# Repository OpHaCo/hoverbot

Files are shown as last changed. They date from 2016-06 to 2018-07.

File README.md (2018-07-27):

# HoverBot : the most affordable smooth and silent two wheels drive control

**NOTE: This project is currently abandoned**  
There is more active development over at https://github.com/NiklasFauth/hoverboard-firmware-hack. We already have a working custom firmware for the hoverboard mainboard, complete with ADC, PPM and Nunchuck control. (See the linked video in the description there)

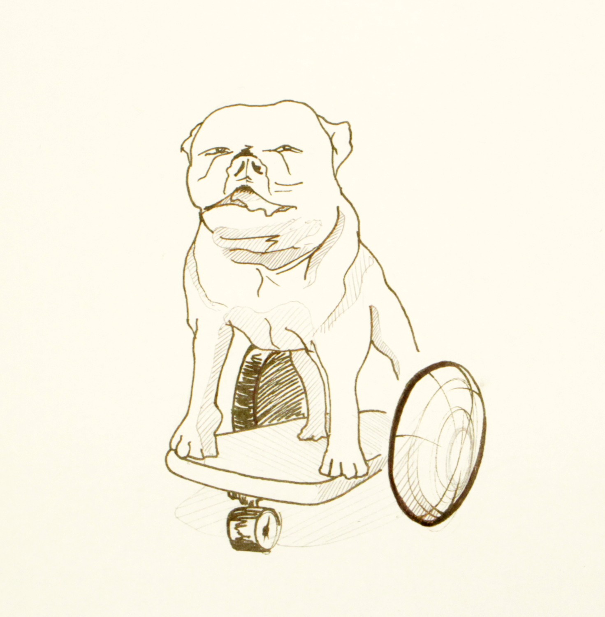
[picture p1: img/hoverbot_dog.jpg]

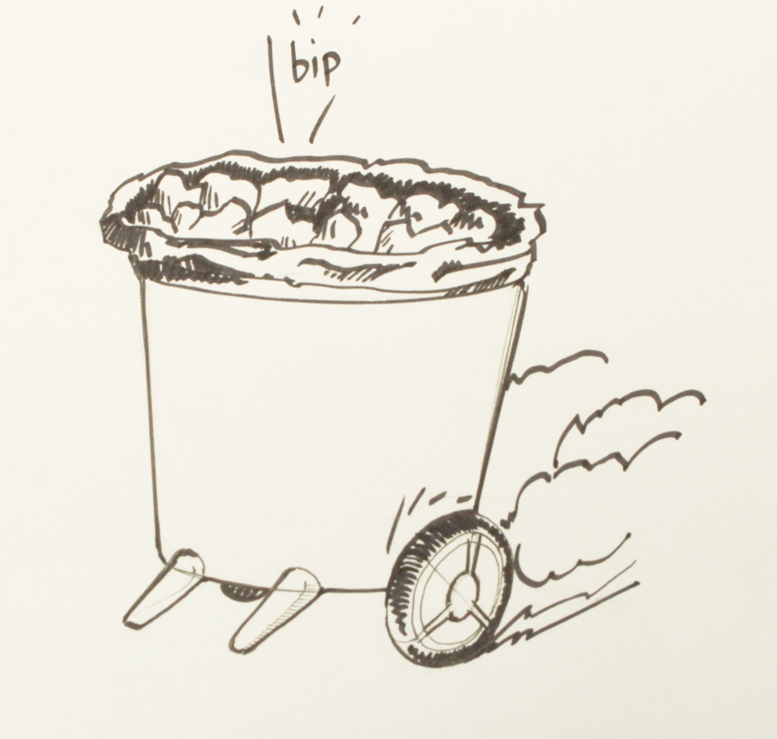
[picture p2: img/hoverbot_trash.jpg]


Project has been done in Amiqual4Home Equipex Creativity Lab - https://amiqual4home.inria.fr/

## **Description**

With hoverbot, you can do some vehicle, chassis :
 * supporting up to 264lbs (120kg). 
 * moving silently thanks to two 350W brushless motors in wheels
 * locally or remotely controlled, 
 * at an unbeatable price buying some spare parts :
    * Mother board - 55  eur
    * 36V battery  - 100 eur
    * two wheels   - 160 eur
    * additional components - 40 eur
    * **Total = 355 eur**
 * or more cheaper :
    * just buy an hoverboard and get these parts from it - 260eur
    * additional components - 40eur
    * **Total = 300eur**

Hoverboard are chinese low cost products. Low cost spare parts gives meaningful two wheels drive platform.

You don't have to be an electronic master to do it. To have motors working, you just have to connect hoverbot shield. You can either make this shield by yourself or you can get it from (TODO).

With hoverbot you will be able to drive your : 
* robot
* chair
* old dog
* couch

## **Prerequisities**

### **hardware**

* [Two hoverboard motors] (http://gyro-service.com/moteur/19-moteur.html)
* [Hoverboard mother board] (http://gyro-service.com/cirquit-carte-mere-smart-self-balancing-wheel/17-carte-mere.html)
* [36V battery] (http://gyro-service.com/batteries-samsung-smart-balance-wheel-gyropode/18-battterie-22p-samsumg-ou-de-qualite-equivalente.html)
* [hoverbot shield](#hoverbot-shield) 
* Arduino Teensy 3.1/3.2

## **Setup**

### **Components Analysis**

Refer [ifixit](http://ifixit.org/blog/7821/swagway-teardown-hoverboards/) for a detailed analysis of hoverboard components.
Interesting parts are :
 * how do these components interact?
 * is it possible to control hoverboard externally?

### **Daughterboard / motherboard communication**

Daughterboard can be used either on right/left. So we only bought 1 daughterboard to decode Daughterboard / motherboard exchanged data.
We connected the 2 motherboard / daughterboard connectors to a single motherboard.
In this case when rotating motherboard, wheels are rotating in two different direction.
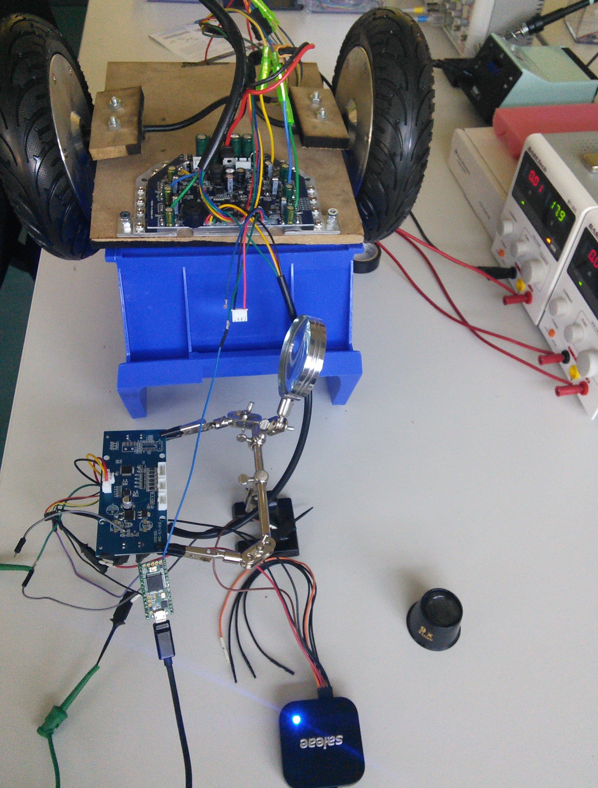
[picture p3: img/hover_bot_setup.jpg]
 

#### **Protocol**
Probing a logic analyser on daughterboard 4 wire connectors gives some interesting info :
 * logic level = 3.3V
 * bit duration ~ 38.10µs => baud rate ~ 26300kbps
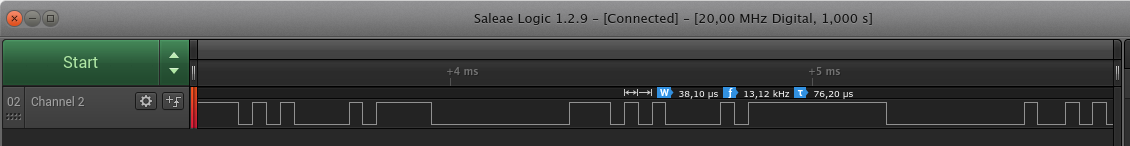
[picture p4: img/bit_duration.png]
 
 * there is no clock provided on given lines => Async protocol 
 
Is it a standard protocol? 
 * may be UART? Some clues can help... Green and yellow lines of daughterboard are connected to [STM32F103](http://www.st.com/content/ccc/resource/technical/document/reference_manual/59/b9/ba/7f/11/af/43/d5/CD00171190.pdf/files/CD00171190.pdf/jcr:content/translations/en.CD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) PA2 - UART2 TX and PA3 - UART3 RX
In order to get UART parameters : 
 * get maximum frame length taking for example a frame of 0 or a frame of 0/1/0/ and so on... After that you will conclude (helped with Salae logic ananlysers):
**Daughterboard send data to motherboard using 3.3V UART @26300bps - 1 stop bit - no parity bit.** 

#### **Exchanged data**

Here are decoded data with  UART analyzer in Salae Logic software :

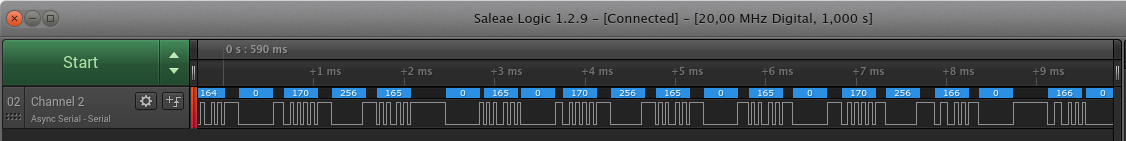
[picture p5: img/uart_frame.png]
 

Do not move daughterboard, power motherboard and read decoded data. We can see :
 * redondant 256 integer : it is frame start => frame size = 6 9bits integers

Now let's play with photodiode used in daughterboard contacts :
 * if we hide at least one of it  last frame integer = 85
 * otherwise last frame integer = 170
If 170 value is sent to motherboard : motors won't be driven (it means user to not have its feet on hoverboard) (it means user to not have its feet on hoverboard)
 
4 remaining bytes must be decoded : two of these bytes repeats.
Rotating daughterboard gives indication :
 * little move only modify a frame integer => this integer must be low significant 9bit 
 * more rotation modifies other integer    => rotation seems to be encoded on 2 9 bit integers.
Rotating around 0 helps us :
**Angular value is coded in 2x9bits signed integer value (2's complement)**

We can check it is only an angular value applying linear acceleration to daughterboard. In this case angular value do not change.

#### ** Speed sensor **
In wheels some hall sensors are used to get wheel speed (3 sensors per wheel).
On mother board, sensor pulses are filtered using an RC filter. To get speed, we must connect it to hoverbot. 

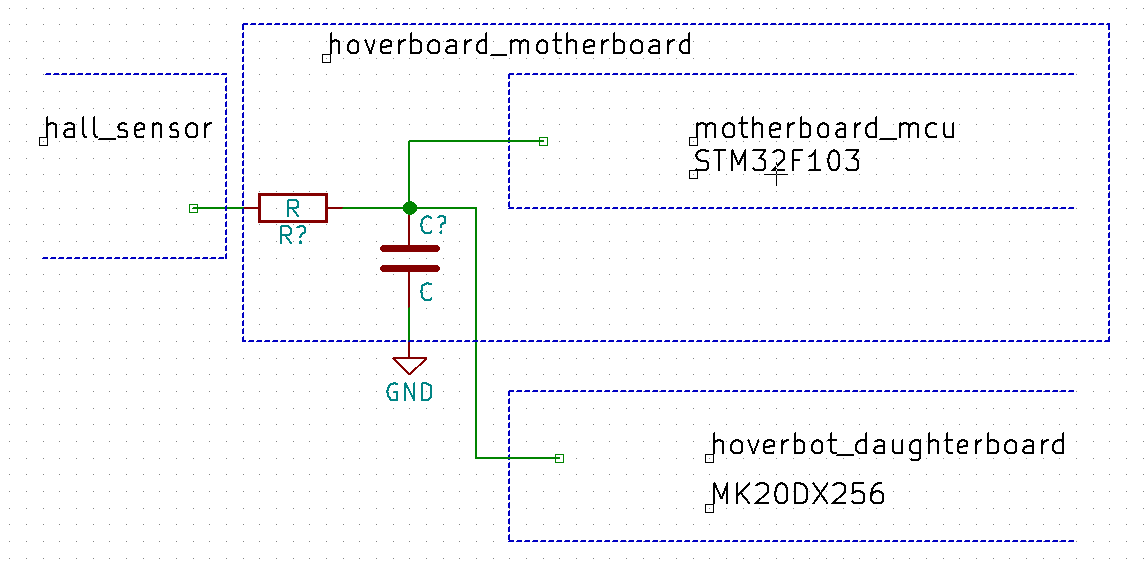
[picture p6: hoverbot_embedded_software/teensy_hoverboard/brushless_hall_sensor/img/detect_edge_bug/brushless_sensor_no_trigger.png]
 

If we trigger a digital output (channel 0) on a rising edge (channel 0) we do not have a clean signal :
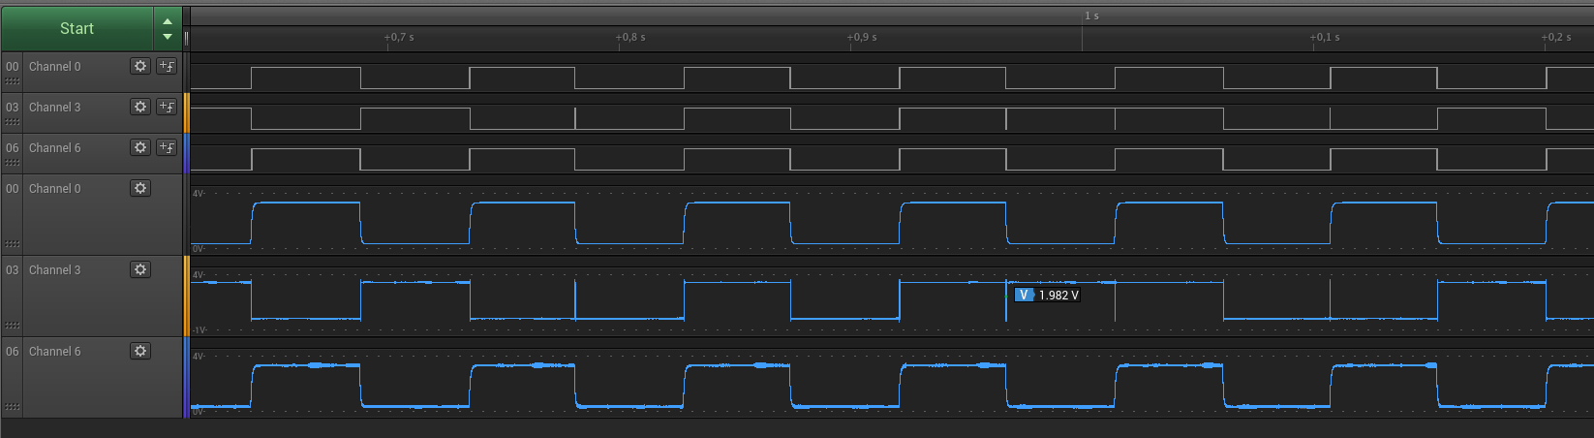
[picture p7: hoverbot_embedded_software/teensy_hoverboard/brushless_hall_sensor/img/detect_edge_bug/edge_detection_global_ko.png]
 

With a zoom :
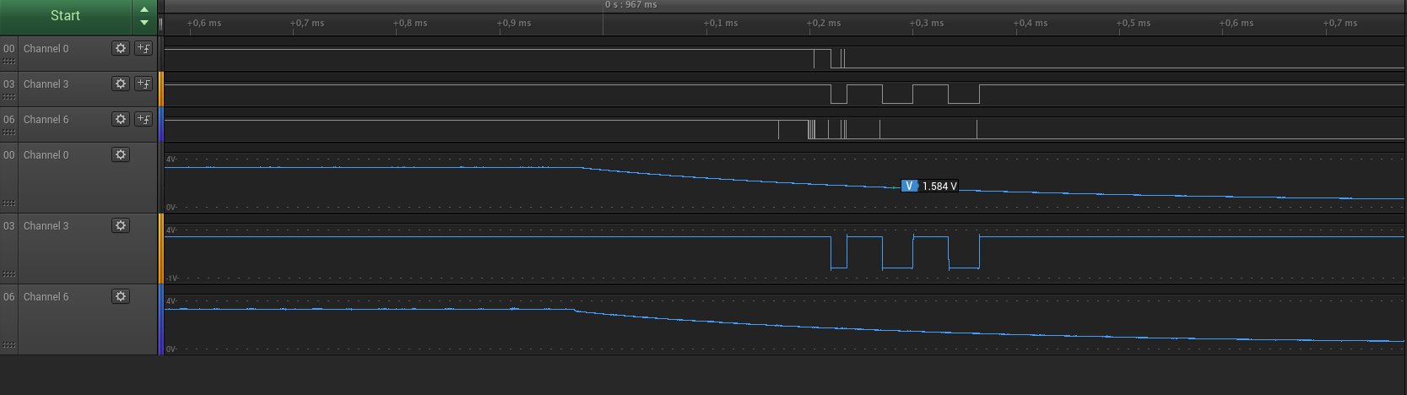
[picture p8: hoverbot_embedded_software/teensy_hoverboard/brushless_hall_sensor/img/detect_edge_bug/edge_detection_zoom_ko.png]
 

Small oscillation when V=Vdd/2 generates some falling /rising edges. Because of RC time constant, we can get lot of oscillations leading to some false detections. It could be software filtered (either using timer or checking multiple times read value). As I prefer capturing Hall sensor pulses using external interrupt it is better to have an hardware solution. As Teensy MCU does not have any input schmitt trigger we will add it :

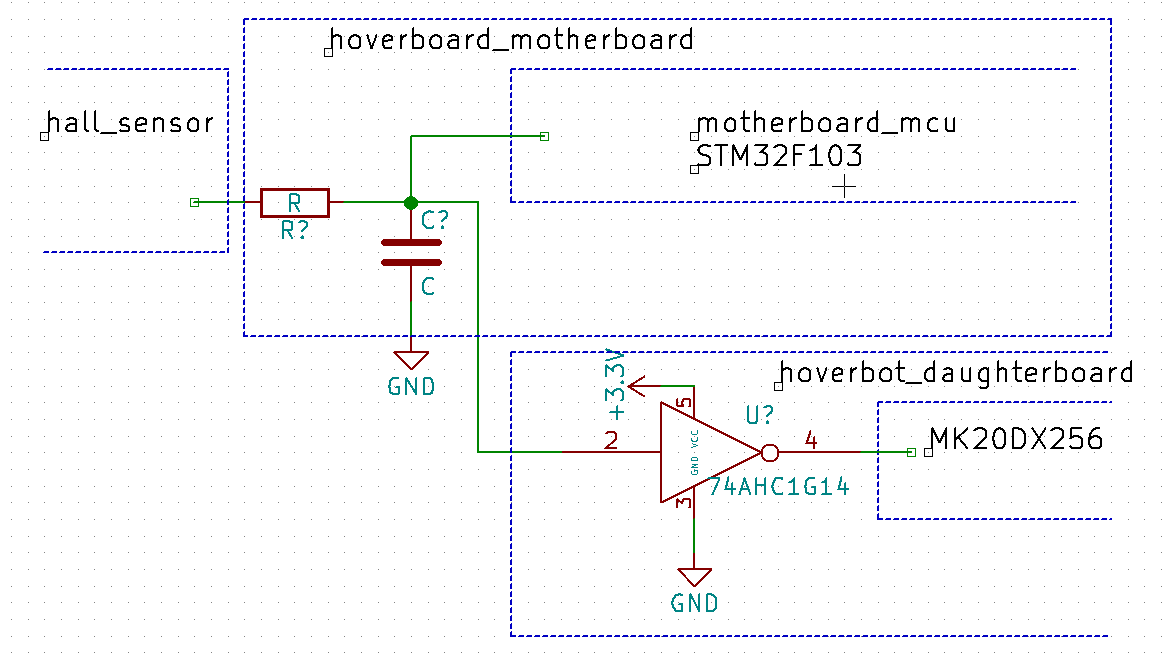
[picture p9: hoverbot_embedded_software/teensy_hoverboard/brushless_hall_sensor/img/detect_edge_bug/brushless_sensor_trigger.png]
 

After we have a good pulse detection :

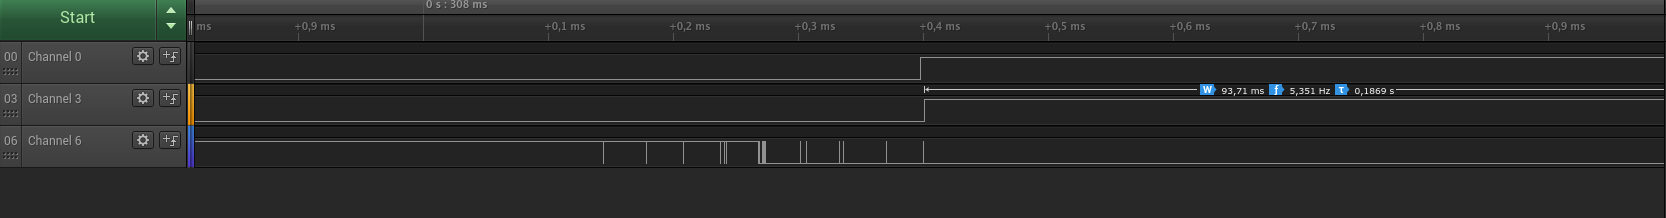
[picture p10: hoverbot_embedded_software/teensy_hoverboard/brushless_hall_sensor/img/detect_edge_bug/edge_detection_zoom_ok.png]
 
 
### **hardware** 

In order to control hoverboard we need an external MCU to :
 * send left and right foot angular position => we need two UART Tx lines supporting 9bits UART @ 26300bps
 * optionally read daughterboard current postion (for tests) => we need 1 UART Rx line supporting 9bits UART @ 26300bps
 
Different MCU can be used, we could use UART bitbanging libraries... But a nice solution is to use teensy 3.1/3.2 :
 * it runs @3.3V
 * [9 bit uart supported on Arduino Core] (https://www.pjrc.com/teensy/td_uart.html)
 * 3 avaialble hardware UARTs!

### **software** 

#### Prerequisities
##### Enable 9-Bit UART on Teensy
Edit :

    your_arduino_core_folder/hardware/teensy/avr/cores/teensy3/HardwareSerial.h

Uncomment :

    #define SERIAL_9BIT_SUPPORT

##### Add needed libraries
Several libraries are provided in this repo : 
 * hoverboard : hoverboard control / feddbacks
 * brushless_hall_sensor
 * logger 

If you use arduino IDE, you must create symlinks/shortcuts from these libraries path to Arduino library folder :

    ln -s your_folder/hoverbot/hoverbot_embedded_software/teensy_hoverboard/hoverboard arduino_user_path/libraries/
    ln -s your_folder/hoverbot/hoverbot_embedded_software/teensy_hoverboard/brushless_hall_sensor arduino_user_path/libraries/
    ln -s your_folder/hoverbot/hoverbot_embedded_software/teensy_hoverboard/logger arduino_user_path/libraries/

Then from Arduino IDE add these libraries.

##### Configure logging level
    
Edit 
    your_folder/hoverbot/hoverbot_embedded_software/teensy_hoverboard/logger/logger_config.h
    
and set needed log level (refer your_folder/hoverbot/hoverbot_embedded_software/teensy_hoverboard/logger/README.md)
    
### Arduino sketch

As we saw in our first tests, when same daughterboard is connected to two motherboards/daughterboard connectors :
 * wheels rotating direction is different. Hoverboard is rotating
In this case same angular value on left foot and right foot is sent to motherboard.
In order to have hoverboard moving forward / backward we must apply for example :
 * a positive angular value on right foot daughterboard Uart
 * negative angular value on left foot daughterboard Uart

From that  simple code is provided here :
[Refer code](https://github.com/OpHaCo/hoverbot/blob/master/hoverbot_embedded_software/teensy_hoverboard/teensy_hoverboard.ino)
In `echoGoForward()`  function : it reads current angular value from daughterboard to control hoverboard in forward direction.

After testing we can easily : 
 * control speed of both wheels when it is rotating in different direction (under load or not)

But we cannot :
 * control speed of both wheels when it is rotating is same directions (not under load). **In this case, motors reach needed value but quickly speed up until max speed**
 
We can suppose, closed loop algorithm on motherboard does not support forward / backward mooving when it is not under load.

## Interfaces
### UART

Hoverboard control over UART can be done running :

    python3 your_folder/hoverbot/hoverbot_gateway_software/examples/hoverboard_uart_control/hoverboard_uart_control.py -p TEENSY_PORT
    
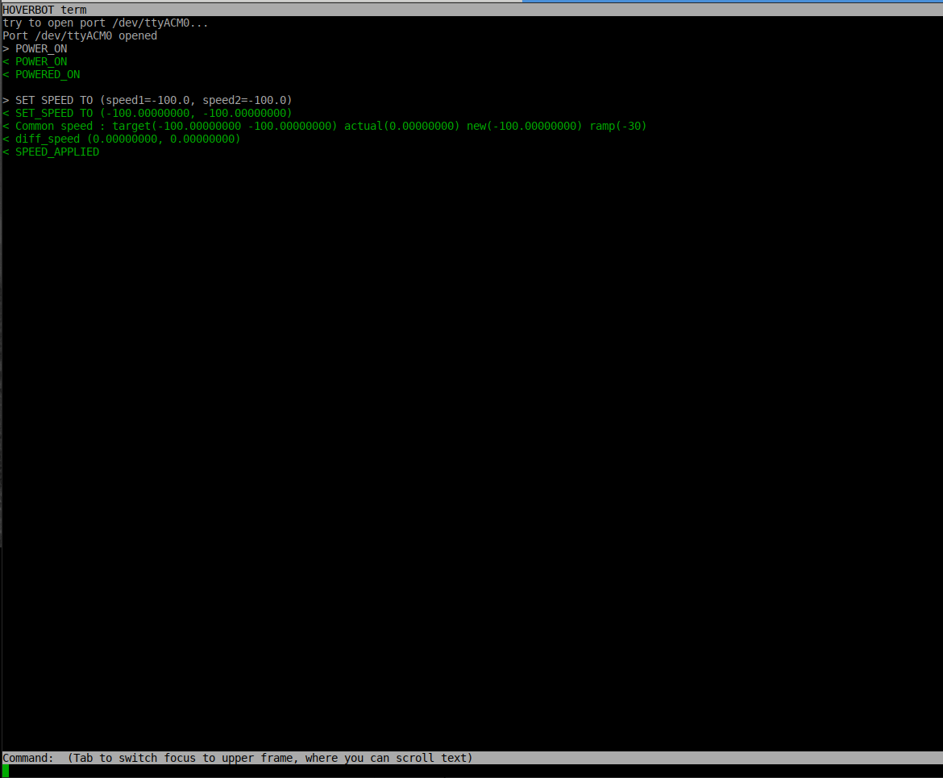
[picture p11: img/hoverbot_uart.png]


#### Supported commands :

    power_on

    power_off
    
    set_speed motor1_value motor2_value
    
    x // Manual keyboard control => hoverbot controlled using numeric pad

### SPI
### Wifi
### BLE

## Commands
TODO

### Control commands
TODO
###ROS
## Events
TODO

## Hoverbot shield
### PCB design

## Examples
### Racing chair

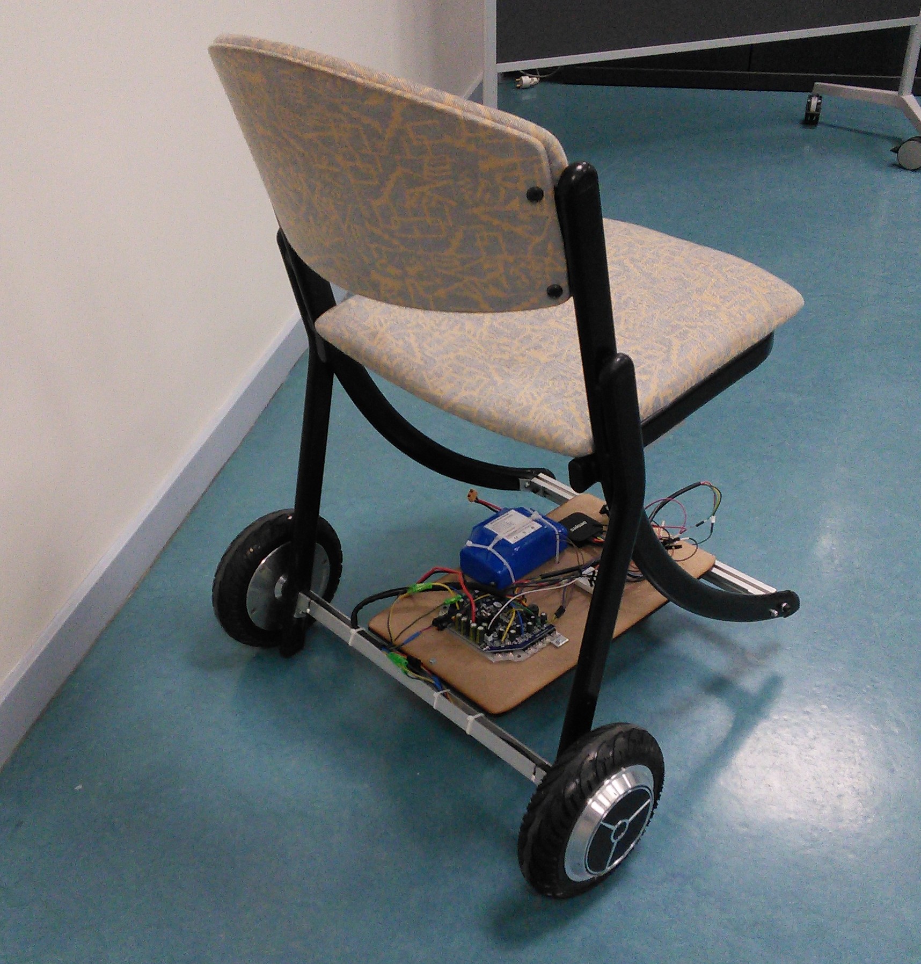
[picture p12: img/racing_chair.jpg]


## Issues

## References
* http://www.electronicspoint.com/threads/reverse-engineering-a-hoverboard-with-wheels-accelerometer.279098/
* http://drewspewsmuse.blogspot.fr/2016/06/how-i-hacked-self-balancing-scooter.html
* https://developer.mbed.org/users/Thomas_H/code/HoverboardTest/

## Next steps

* improve hoverboard control
* continue cleaning (remove some unused attributes in hoverboard)
* add PID : measure reliable speed from hall sensors
* use all days a reliable racing chair
* make hoverbot shield : deliver CAD
* ROS compatible?
* get error status

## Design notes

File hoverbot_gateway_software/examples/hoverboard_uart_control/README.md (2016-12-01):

# Description
Example of hoverboard UART control.

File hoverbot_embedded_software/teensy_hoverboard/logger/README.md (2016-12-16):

## logging

### Overview

Logging library, supports a variable list of arguments and its format specifiers. 
Log level can be modified according to user needs. 
Using preprocessor logging macros defined in logger.h reduces code size depending on selected logger level.

#### Supported targets

  * MCU having Arduino software (Stream, Serial...)

####Log levels
 * LOG_LEVEL_NOOUTPUT 
 * LOG_LEVEL_ERRORS 1
 * LOG_LEVEL_INFOS 2
 * LOG_LEVEL_DEBUG 3
 * LOG_LEVEL_VERBOSE 4

#### Code snippet
Log using a software serial stream.

    #include <logger.h>
    #include <AltSoftSerial.h>
    
    #define LOG_LEVEL LOG_LEVEL_DEBUG
    
    static AltSoftSerial altSerial;

    void setup()
    {
        Serial.begin(115200);
        altSerial.begin(9600);
        
        LOG_INIT(LOG_LEVEL, &altSerial);
	    LOG_INFO(F("application started ! \n"));
    }

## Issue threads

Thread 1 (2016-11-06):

Speed control loop

tyler123durden, 2016-11-06:
Hello,
I've also started with some hoverboard hacks, here are my projects:
https://github.com/tyler123durden/hoverboard-hardware
https://developer.mbed.org/users/Thomas_H/code/HoverboardTest/

I started some tests with a closed loop control for the speed. But at certain points I've got some strange behaviour. Especially when wheels should rotate in different directions or speeds. It is possible to do this but control loop behaves kind of sluggish. Do you have done such tests?
Here are some diagrams:
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

Lahorde, 2016-11-17:
As you can see, in my sketch I control both motors. I can :

* rotate cleanly motor 1 in clockwise while motor 2 is in other direction (in this case, I send same angle values to mother board)
* rotate cleanly motor 1 in non-clockwise while motor 2 is in other direction (in this case, I send same angle values to mother board)
in these configurations, I can control motor speed.

But when I have both motors rotating in same direction (in this case I give a positive angular position on left daughterboard UART and a negative one on right daughterboard UART), first it rotates well, but after some seconds, it speeds up until reaching max speed. I think something misses in this case. It's quite strange, I'm wondering if my motherboard is not buggy. May be solution is elsewhere : calibration, other sensor...
I've tried different calibrations values and it dit not change anything. I told Drew Nibble if he got same issue and he said "I believe that the acceleration when both wheels are going the same direction is a bug in the closed loop controller. It does not seem to happen under load (although I have not tested extensively)"
 I must test this hypothesis on a true hoverboard! May be you have tested it?

So I should get in few days a new motherboard : http://www.skywalkers.paris/pieces-detachees-hoverboard/91-carte-mere-taotao-hoverboard-adulte-7091046701306.html
and an hoverboard.

I think we want to make same thing : closed loop speed control using this cheap motherboard, and I'm sure we will manage to do it!

tyler123durden, 2016-11-17:
OK, I see. In my tests same direction means different sign for both sides and different direction (hoverboard rotates) means same sign.
The motor board seems to have kind of PI characteristic. As you see in same direction plot. You have to reduce input to 0 or nearly to hold same speed. I think this is your speed up at constant input.
But this does not apply for different directions (same sign). Here it has more kind of P characteristic. Which does also apply if both wheel speeds differ to much then.
Will try to get some plots for open loop speed response. But maybe I've got another firmware version because I must send following sequence, which has 2 more bytes.

            oMotorRight.putc(256);
            oMotorRight.putc(_Controlloop[RIGHT].u & 0xFF);
            oMotorRight.putc((_Controlloop[RIGHT].u >> 8) & 0xFF);
            oMotorRight.putc(_Controlloop[RIGHT].u & 0xFF);
            oMotorRight.putc((_Controlloop[RIGHT].u >> 8) & 0xFF);
            oMotorRight.putc(85);
            oMotorRight.putc(82);
            oMotorRight.putc(82);

I've not tested my setup under load, will try to test it that weekend.

Lahorde, 2016-11-17:
" As you see in same direction plot. You have to reduce input to 0 or nearly to hold same speed.", that's it, above a given threshold, speeds keeps increasing until reaching max speed. You are true with PI behaviour, but physically, it's quite hard to understand, but I think it's because I never rode an hoverboard. Maybe in forward direction, rotating feets rotate first gyroscope daughterboards causing hoverboard speed up, maybe during this acceleration gyroscope daughteboards come back to a flat position... I should test it in some few days!

Lahorde, 2016-11-17:
I will test tomorrow an integral control,
In pseudo code :

    setForwardSpeed(speed)
       setRightSpeed(speed*ramp_up_coef)
       setLeftSpeed(speed*ramp_up_coef)
       startTimer(duration = 1/ramp_up_coeff)

    onTimerExpired()
       setRightSpeed(0 calibration value)
       setLeftSpeed(0 calibration value)

Lahorde, 2016-11-18:
Got it and tested :
```
/**
 * Integral control of speed
 */
void goForward(uint16_t speed)
{
  float RAMP_UP_FACTOR = 1;
  uint16_t  speedRampUp = (speed*RAMP_UP_FACTOR);

  uint16_t lFrame[6] = {256, speedRampUp & 0xff, speedRampUp >> 8 & 0xff, speedRampUp & 0xff, speedRampUp >> 8 & 0xff, 85};
  uint16_t rFrame[6] = {256, (-speedRampUp) & 0xff, (-speedRampUp) >> 8 & 0xff, (-speedRampUp) & 0xff, (-speedRampUp) >> 8 & 0xff, 85};

  Serial.print(millis());
  Serial.print(": applying speed of ");
  Serial.println(speedRampUp);

  uint32_t timeStart = millis();
  while((millis() - timeStart) < (1/RAMP_UP_FACTOR)*10000)
  {
    for(uint8_t index = 0; index < 6; index++)
    {
      DAUGHTER_BOARD_SERIAL_SIM_R.write9bit(rFrame[index]);
      DAUGHTER_BOARD_SERIAL_SIM_L.write9bit(lFrame[index]);
    }
  }

  speedRampUp = _calValue;

  lFrame[1] = _calValue & 0xff;
  lFrame[2] = _calValue >> 8 & 0xff;
  lFrame[3] = lFrame[1];
  lFrame[4] = lFrame[2];

  rFrame[1] = -_calValue & 0xff;
  rFrame[2] = -_calValue >> 8 & 0xff;
  rFrame[3] = rFrame[1];
  rFrame[4] = rFrame[2];

  Serial.print(millis());
  Serial.print(": applying speed of ");
  Serial.println(_calValue);

  while(1){
    for(uint8_t index = 0; index < 6; index++)
    {
      DAUGHTER_BOARD_SERIAL_SIM_R.write9bit(rFrame[index]);
      DAUGHTER_BOARD_SERIAL_SIM_L.write9bit(lFrame[index]);
    }
  }
}
```

In order to get clean control we must also hack calibration process to have a 0 calibration!

Lahorde, 2016-11-18:
Look at https://github.com/OpHaCo/hoverbot/blob/master/hoverbot_embedded_software/teensy_hoverboard/teensy_hoverboard.ino for an updated code. Some work in code must be done to have a clean control, I will close issue when I will finish it.

tyler123durden, 2016-11-18:
Great to see it works!
So maybe you could also try controlling both wheels with different speeds and look at the response.
For the calibration process if would guess all is done in the motor controller and no communication to the gyro board is done. The motor board just sets the zero point to the received gyro inputs. So just send 0 to the motorboard and start calibration should do the trick.
As mentioned above a simple PI controller works quite good for speed control except if wheel speed differs to much.

Lahorde, 2016-11-19:
Yes, calibration can definitely been done manually, as you said,  just set a 0 output on your MCU UARTs when you do calibration. Next week I will test it deeper, integration factor must be precisely identified.

KevinPlaridel, 2016-12-11:
Hello Lahorde. I've been trying to make my hoverboard works and I tried your sketch, but there is error. Can you help me?

I put the hoverboard.h and brushless_hall_sensor.h in
C:\Program Files (x86)\Arduino\hardware\teensy\avr\cores\teensy3

but the error is
```
C:\Program Files (x86)\Arduino\hardware\teensy\avr\cores\teensy3\hoverboard.cpp:81:33: error: 'SERIAL_9N1' was not declared in this scope
   _p_gyro1Serial->begin (26300, SERIAL_9N1);  // 9 bits mode
                                 ^
C:\Program Files (x86)\Arduino\hardware\teensy\avr\cores\teensy3\hoverboard.cpp: In member function 'Hoverboard::EHoverboardErr Hoverboard::setSpeed(float, float)':
```

Hope you can help. Thank you

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

KevinPlaridel, 2016-12-11:
SERIAL_9N1 is solved. but when I added
```
#include <hoverboard.h>
#include <brushless_hall_sensor.h>
```
"idlecontrol() was not declared" said in the error

```
hoverboard_original:36: error: 'idleControl' was not declared in this scope
     idleControl();
```

Lahorde, 2016-12-16:
I've updated code, refer https://github.com/OpHaCo/hoverbot/blob/master/hoverbot_embedded_software/teensy_hoverboard/hoverboard/hoverboard.cpp
I've not yet implemented any PID. Some coding / cleaning must still be done but now everything is possible. Next step is to improve hoverboard control and to make an hoverbot shield.

Closed 2016-12-16.

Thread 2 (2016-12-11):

Error Compiling

KevinPlaridel, 2016-12-11:
I can't compile the sketch because there's an error to hoverboard.cpp and idlecontrol().
I added the .cpp and .h in

> C:\Program Files (x86)\Arduino\hardware\teensy\avr\cores\teensy3

this is the error:
```
In file included from C:\Users\Kevin\Documents\School\thesis\sketch\hoverboard\hoverboard.ino:2:0:

C:\Program Files (x86)\Arduino\hardware\teensy\avr\cores\teensy3/hoverboard.cpp: In member function 'Hoverboard::EHoverboardErr Hoverboard::init()':

C:\Program Files (x86)\Arduino\hardware\teensy\avr\cores\teensy3/hoverboard.cpp:81:33: error: 'SERIAL_9N1' was not declared in this scope

   _p_gyro1Serial->begin (26300, SERIAL_9N1);  // 9 bits mode

                                 ^

C:\Program Files (x86)\Arduino\hardware\teensy\avr\cores\teensy3/hoverboard.cpp: In member function 'Hoverboard::EHoverboardErr Hoverboard::setSpeed(float, float)':

....

Error compiling for board Teensy 3.2 / 3.1.
```

Lahorde, 2016-12-11:
Open :

    your_arduino_core_folder/hardware/teensy/avr/cores/teensy3/HardwareSerial.h

Uncomment

    #define SERIAL_9BIT_SUPPORT

Closed 2016-12-11.

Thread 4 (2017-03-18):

Documentation of power button and stat wiring

MaxZZZZZZ, 2017-03-18:
Thanks for the code that you provided, it's very useful.
One thing that is missing in the README is how you wired power button and status LED. Can you please add it or at least respond in this issue?

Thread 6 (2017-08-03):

OpenSource firmware for motor control on the STM32F103

casainho, 2017-08-03:
Hi, great project!!

I developed OpenSource firmware for motor control using the STM32F103, for electric unicycles. Currently I am developing for the cheap chinese ebike controllers, one based on STM8 and other with STM32F103.

Would be great if you or someone could develop firmware for the motor control for the hoverboards.

But my target is to make firmware for cheap ebike Kunteng STM8 controllers and make them a general bldc motor controller - it has UART communication and so with an Arduino, anyone could control easily this type of motors.

https://opensourceebikefirmware.bitbucket.io/

https://eggelectricunicycle.bitbucket.io/

LeoDJ, 2017-09-10:
I would really like to delve into developing a BLDC controller on the hovervoard mainboard.
But I do not know how to best get started and not brick and/or fry the motherboard. E.g. if I would activate the wrong outputs, the MOSFETs would short the battery and something will explode.

Also I'm not quite sure how I would then implement the BLDC controller using the hall effect sensor inputs.

I guess, that you have way more experience with those things, seeing that you already wrote such a firmware for the STM, only driving one motor.

Maybe we could work together on this? I am currently in the process of reverse engineering the mainboard (getting the pinout of the mosfets etc)

casainho, 2017-09-10:
Hi.

_Maybe we could work together on this? I am currently in the process of reverse engineering the mainboard (getting the pinout of the mosfets etc)_
I am not motivated to work on the hoverboard: I look to them as a toy because are instable after 10km/h; I would prefer electric unicycles that can go over 30km/h (yes, I did ride both of them). But now I even prefer electric bicycles because they are way safe than electric unicycles at speeds like 25km/h and over than. I usually ride at up to 45km/h, on flat land were I live.

My focus is to develop OpenSource firmware for the cheap and widely available EBike motor controllers. The one I am developing for now, costs only 14€!! It has UART interface for an LCD or bluetooth modules. My plan is to create a generic motor controller that can be commanded by Arduino, using the UART interface, then anyone will be able to this motor controllers and do oter devices like hoverboard, electric unicycles, etc!!

I have an idea for you: use the Lishui LSW-675 EBike motor controller that is relative cheap and uses the same STM32FEBKC6T6 as on the hoverboard -- you can find the datasheet of STM32FEBKC6T6 here as many other information: https://opensourceebikefirmware.bitbucket.io/Motor_controllers--Lishui_motor_controllers--LSW-675.html

Good luck and don't forget to start a thread on https://endless-sphere.com/forums/viewforum.php?f=30 to document and post news about this project!!

LeoDJ, 2017-09-28:
Okay. On terms of hoverboard riding, we are on the same page. I don't want to use it in its original form, but repurpose the motors, main board and battery as a drive chain for a few robot ideas I have in mind, because they are still very powerful.
I think I found the [official firmware](https://github.com/EGG-electric-unicycle/bldc_chinese_firmware_2) for the hoverboard mainboard, so it hopefully shouldn't be so hard to reprogram it to accept direct control commands over UART.

Thanks for the tip with the LSW-675. It's too expensive for me to use as an ESC for the two motors, but I'll look into the firmware for inspiration.

As for the 14€ open source motor controller: That sounds really neat, I'll look forward to using that in the future 😉

casainho, 2017-09-28:
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
Don't you want to join the project?? we can implement the firmware for a
generic motor controller that is controlled using UART commands send by
Arduino.

--
Cumprimentos,
Jorge Pinto
E-mail: casainho@gmail.com
Telemóvel: 927145983

LeoDJ, 2017-09-28:
Yeah, good idea.
Currently I'm a little bit busy with uni, but I'll see when I got time :D
What do you think is the best way we can communicate?

casainho, 2017-09-28:
We use the forum, see on the project page the link.

Em 28/09/2017 16:39, "Leandro Späth" <notifications@github.com> escreveu:

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

chulo601, 2017-10-14:
LeoDJ i have over 50+ hoverboard i can give for free just pay for shipping so you can test the reprogramming of the hoverboard. I will like to use the hoverboard main board and be able to control both wheels with arduino.
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

LeoDJ, 2017-10-14:
Wow, that sounds awesome! It would be neat to have one or two that I can test my code on, without the fear that I would be bricking one beyond repair ^^
How much would shipping to Germany cost?

VladimirAkopyan, 2017-11-02:
this is very amusing

ScottEllisNovatex, 2018-05-01:
See https://github.com/NiklasFauth/hoverboard-firmware-hack

vetalik08, 2018-05-28:
Have any more hover boards your willing tk donate if I paid for shipping?

eric-schleicher, 2018-06-06:
@chulo601 is this still an area of interest for you?  I have a number of interns that are interested making a balance bot from these component. let me know if there is still a supply of yunked parts.  we're in US, would certainly pay for shipping.

casainho, 2018-06-11:
I implemented FOC using as input: battery voltage; actual duty_cycle; battery current read on shunt; motor speed in ERPs measured on hall sensors; motor inductance.

Videos and realtime graphs, etc:
- https://www.endless-sphere.com/forums/viewtopic.php?p=1385495#p1385495
- https://www.endless-sphere.com/forums/viewtopic.php?p=1385495#p1385553

The only parameter that depends from the motor is the motor inductance L. The math is:
angle = arc sin (I motor phase * W * L / V motor phase).
I motor phase: battery current read on shunt / duty_cycle
V motor phase: battery voltage * duty_cycle

The piece of code:
  //************************************************************************************
  // FOC implementation by calculating the angle between phase current and rotor magnetic flux (BEMF)
  // 1. phase voltage is calculate
  // 2. I*w*L is calculated, where I is the phase current. L was a measured value for 48V motor.
  // 3. inverse sin is calculated of (I*w*L) / phase voltage, were we obtain the angle
  // 4. previous calculated angle is applied to phase voltage vector angle and so the
  // angle between phase current and rotor magnetic flux (BEMF) is kept at 0 (max torque per amp)

  // calc E phase voltage
  ui16_temp = ui16_adc_battery_voltage_filtered * ADC10BITS_BATTERY_VOLTAGE_PER_ADC_STEP_X512;
  ui16_temp = (ui16_temp >> 8) * ui8_duty_cycle;
  ui16_e_phase_voltage = ui16_temp >> 9;

  // calc I phase current
  if (ui8_duty_cycle > 10)
  {
    ui16_temp = ui16_adc_battery_current_filtered * ADC_BATTERY_CURRENT_PER_ADC_STEP_X512;
    ui32_i_phase_current_x2 = ui16_temp / ui8_duty_cycle;
  }
  else
  {
    ui32_i_phase_current_x2 = 0;
  }

  // calc W angular velocity: erps * 6.3
  ui32_w_angular_velocity_x16 = ui16_motor_speed_erps * 101;

  // 36V motor: L = 76uH
  // 48V motor: L = 135uH
  ui32_l_x1048576 = 142; // 1048576 = 2^20

  // calc IwL
  ui32_temp = ui32_i_phase_current_x2 * ui32_l_x1048576;
  ui32_temp *= ui32_w_angular_velocity_x16;
  ui16_iwl_128 = ui32_temp >> 18;

  // calc FOC angle
  ui8_foc_angle = asin_table (ui16_iwl_128 / ui16_e_phase_voltage);

  // low pass filter FOC angle
  ui16_foc_angle_accumulated -= ui16_foc_angle_accumulated >> 4;
  ui16_foc_angle_accumulated += ui8_foc_angle;
  ui8_foc_angle_filtered = ui16_foc_angle_accumulated >> 4;

  // apply FOC angle
  ui8_foc_angle_correction = -ui8_foc_angle_filtered;
  //************************************************************************************

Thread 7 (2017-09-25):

Hoverboard shield

hermanbanken, 2017-09-25:
Hi guys,
For a hackathon I'm currently figuring out what is gonna drive our (potentially large/heavy) robot, so I'm looking beyond robot chassis and looking to this kind of projects. Unfortunately I'm no electronisch expert, so I'm relying on what I can find here and there.

Do I get it right that you intent to design a shield and this image contains the prototype on the breadboard?
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

Could you share a photo where you can see the actual breadboard? Also is it correct you have a Logic Analyzer on there? Is it required?

Hope you can share some more of your efforts!

plguhur, 2017-11-02:
Hello guys, I am looking quite for the same thing: the hoverbot shield. Did you publish your PCB design?

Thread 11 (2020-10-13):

driving one motor

setaretavakoli, 2020-10-13:
hi
could you help us to drive only one motor?
because doe to our search the controller circuit needs both of the motors to have a close circuit.
pls. correct us if we're wrong.
you can contact us with :
kakimia595@gmail.com or f.tavakoli9273@gmail.com

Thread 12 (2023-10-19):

Denver need help

r3k0sa, 2023-10-19:
Hey maybe sameone have model:DBO-10000 mk3 software? I made a mistke when trying edit and make it with remote control... i dont saved software and now its not working so plz if someone have send it to me 🙏
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

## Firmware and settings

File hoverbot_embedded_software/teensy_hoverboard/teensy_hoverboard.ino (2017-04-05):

/******************************************************************************
 * @file    hoverboard sketch
 * @author  Rémi Pincent - INRIA
 * @date    28/11/2016
 *
 * @brief Hoverboard sketch example to control hoverboard.
 *  
 * Project : hoverbot
 * Contact:  Rémi Pincent - remi.pincent@inria.fr
 *
 * Revision History:
 * https://github.com/OpHaCo/hoverbot.git
 * 
 * LICENSE :
 * hoverbot (c) by Rémi Pincent
 * project_name is licensed under a
 * Creative Commons Attribution-NonCommercial 3.0 Unported License.
 *
 * You should have received a copy of the license along with this
 * work.  If not, see <http://creativecommons.org/licenses/by-nc/3.0/>.
 *****************************************************************************/

/**************************************************************************
 * Include Files
 **************************************************************************/
#include <logger_config.h>
#include <hoverboard.h>
#include <brushless_hall_sensor.h>

/**************************************************************************
 * Manifest Constants
 **************************************************************************/
#define LOG_SPEED 500000
#define LOG_SERIAL Serial
#define MAX_CMD_LENGTH 0xFFU

#define SET_SPEED_CMD_LENGTH 13U 
#define POWER_ON_CMD_LENGTH   1U 
#define POWER_OFF_CMD_LENGTH  1U 
#define STOP_CMD_LENGTH       1U 
/**************************************************************************
 * Type Definitions
 **************************************************************************/
/*****************************************
 * CONTROL cmd format
 *  __________________________________
 * |       |             |            |
 * |CMD_ID | CMD_PARAMS  | TODO CRC   |
 * |_______|_____________|____________|
 * 
 ****************************************/
typedef enum
{
  SET_SPEED    = 0, /* ARGS : SPEED1 (short LE) - SPEED2 (short LE) */
  POWER_ON     = 1,
  POWER_OFF    = 2,
  STOP         = 3
}EControlCmd;

typedef enum
{
  ACK          = 0,
  SPEED_STATUS = 1
}EFeedbackCmds;

typedef enum
{
  ACK_OK        = 0, 
  ACK_BAD_STATE = 1
}ECmdAckType;

/**
 * Class that listen hoverboard commands over UART to control it.
 */
class HoverboardListenerExample : public HoverboardListener
{
  public:
    HoverboardListenerExample(Hoverboard* );
    void init(void);
    void calibrateHoverboard(void);
    void onSpeedChanged(float arg_f_motor1Speed, float arg_f_motor2Speed);
    void onSpeedApplied(void);
    void onPowerOn(void);
    void onPowerOff(void);
    void pollCmd(void);
    void sendCmd(EFeedbackCmds arg_e_cmdType, uint8_t arg_au8_cmd[], uint8_t arg_u8_cmdLength);
    
  private:
    void waitKey(uint8_t arg_u8_key);
    void handleCommand(uint8_t arg_u8_cmd[], uint16_t arg_u16_cmdLength);

  private:
    Hoverboard* _p_hoverboard;
};

/**************************************************************************
 * Static variables definitions
 **************************************************************************/
static uint8_t _au8_rcvCmd[MAX_CMD_LENGTH] = {0};

/** ItCBS will be filled by hoverboard */
static BrushlessHallSensor::ItCbs motor1ItCbs;

/** Hall sensor 1 - Give pin here */
static BrushlessHallSensor::Config _hallSensor1Conf(17, 18, 19, motor1ItCbs);

/** ItCBS will be filled by hoverboard */
static BrushlessHallSensor::ItCbs motor2ItCbs;

/** Hall sensor 2 - Give pin here */
static BrushlessHallSensor::Config _hallSensor2Conf(13, 14, 15, motor2ItCbs);

static Hoverboard::Config _hoverboardConf(20, 
  21,
  &_hallSensor1Conf,
  &_hallSensor2Conf,
  Serial1,
  Serial3);

static Hoverboard _hoverboard(_hoverboardConf);
static HoverboardListenerExample _hoverboardListenerExample(&_hoverboard);
/**************************************************************************
 * Global functions Definitions
 **************************************************************************/
void setup() {
   LOG_SERIAL.begin(500000);
   LOG_INIT_STREAM(LOG_LEVEL, &LOG_SERIAL);
   /** Wait 1s to get setup logs */
   delay(2000);
   LOG_INFO_LN("starting hoverboard hack...");
   _hoverboard.init();
   _hoverboardListenerExample.init();
}

void loop() {
  _hoverboard.idleControl();
  
  _hoverboardListenerExample.pollCmd();
}

/**************************************************************************
 * HoverboardListenerExample Definitions
 **************************************************************************/

HoverboardListenerExample::HoverboardListenerExample(Hoverboard* arg_p_hoverboardExample)
{
  _p_hoverboard = arg_p_hoverboardExample;
}

void HoverboardListenerExample::init(void)
{
  _p_hoverboard->registerListener(this);
}

void HoverboardListenerExample::onSpeedChanged(float arg_f_motor1Speed, float arg_f_motor2Speed)
{
  LOG_INFO_LN("New speed (%f, %f)", arg_f_motor1Speed, arg_f_motor2Speed);   
}

void HoverboardListenerExample::onSpeedApplied(void)
{
  LOG_INFO_LN("SPEED_APPLIED"); 
}

void HoverboardListenerExample::onPowerOn(void)
{
  LOG_INFO_LN("POWERED_ON"); 
}

void HoverboardListenerExample::onPowerOff(void)
{
  LOG_INFO_LN("POWERED_OFF"); 
}

void HoverboardListenerExample::waitKey(uint8_t arg_u8_key)
{
  while(1) 
  {
    _p_hoverboard->idleControl();
    if(LOG_SERIAL.available() && LOG_SERIAL.read() == arg_u8_key)break;
  }
}

/**
 * Manual calibration : user must refer instructions on UART
 */
void HoverboardListenerExample::calibrateHoverboard(void)
{
  LOG_INFO_LN("Hoverboard calibration");
  LOG_INFO_LN("Power off hoverboard - press enter when done");
  waitKey('\r');

  LOG_INFO_LN("Power on hoverboard - press enter when done");
  waitKey('\r');
  
  LOG_INFO_LN("Press hoverboard button during a time given in hoverboard manual - press enter when done");
  waitKey('\r');
  
  LOG_INFO_LN("Calibrating...");
   
  /** 5s calibration */
  uint32_t loc_u32_time = millis();
  while(millis() - loc_u32_time < 7000)
  {
    _p_hoverboard->idleControl();
  }
  LOG_INFO_LN("Calibration done - press hoverboard button during a time given in hoverboard manual to exit calibration - press enter when done");
  waitKey('\r');
}

void HoverboardListenerExample::pollCmd(void)
{
  uint16_t loc_u16_cmdLength = 0;
  while(LOG_SERIAL.available())
  {
    if(loc_u16_cmdLength > MAX_CMD_LENGTH)
    {
       LOG_ERROR("Invalid command length");
       return;
    }
    _au8_rcvCmd[loc_u16_cmdLength++] = LOG_SERIAL.read();
  }

  if(loc_u16_cmdLength > 0)
  {
    handleCommand(_au8_rcvCmd, loc_u16_cmdLength);
  }
}

void HoverboardListenerExample::sendCmd(EFeedbackCmds arg_e_cmdType, uint8_t arg_au8_cmd[], uint8_t arg_u8_cmdLength)
{
  //TODO
}

void HoverboardListenerExample::handleCommand(uint8_t arg_u8_cmd[], uint16_t arg_u16_cmdLength)
{
  if(arg_u8_cmd[0] == POWER_ON && arg_u16_cmdLength == POWER_ON_CMD_LENGTH)
  {
    LOG_INFO_LN("POWER_ON");
    _p_hoverboard->powerOn();
  }
  else if(arg_u8_cmd[0] == POWER_OFF && arg_u16_cmdLength == POWER_OFF_CMD_LENGTH)
  {
    LOG_INFO_LN("POWER_OFF");
    _p_hoverboard->powerOff();
  }
  else if(arg_u8_cmd[0] == SET_SPEED && arg_u16_cmdLength == SET_SPEED_CMD_LENGTH)
  {
    /** Data in little endian */
    float _speed1, _speed2;
    uint32_t _rampUpDur;
    uint32_t temp_val = arg_u8_cmd[1] | 
      arg_u8_cmd[2] << 8  |
      arg_u8_cmd[3] << 16 |
      arg_u8_cmd[4] << 24;
      
    _speed1 = *(float*)(&temp_val);
    
    temp_val = arg_u8_cmd[5] | 
      arg_u8_cmd[6] << 8  |
      arg_u8_cmd[7] << 16 |
      arg_u8_cmd[8] << 24;

    _speed2 = *(float*)(&temp_val);

    _rampUpDur = arg_u8_cmd[9] | 
      arg_u8_cmd[10] << 8  |
      arg_u8_cmd[11] << 16 |
      arg_u8_cmd[12] << 24;

    if(_rampUpDur <= 0)
    {
      LOG_ERROR("Invalid ramp up duration given");
    }
    else
    {
      LOG_INFO_LN("SET_SPEED TO (%f, %f) in %d ms",
        _speed1,
        _speed2,
        _rampUpDur);
      _p_hoverboard->setSpeedAsync(_speed1, _speed2, _rampUpDur); 
    }
  }
  else if(arg_u8_cmd[0] == STOP && arg_u16_cmdLength == STOP_CMD_LENGTH)
  {
    LOG_INFO_LN("STOP TODO");
  }
  else
  {
    LOG_INFO_LN("Command %d of length %d not handled",
      arg_u8_cmd[0],
      arg_u16_cmdLength);
  }
}

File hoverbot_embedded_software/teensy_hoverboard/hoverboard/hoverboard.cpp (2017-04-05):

/******************************************************************************
 * @file    hoverboard.cpp
 * @author  Rémi Pincent - INRIA
 * @date    28/11/2016
 *
 * @brief Hoverboard implementation. Hoverboard control done hacking : 
 *  - gyroscope daughterboards signals to control speed
 *  - power button
 *  - Brushless motors Hall sensors (3 per motors)
 *  - Status LED to get ERROR signal
 *  
 * Requires : 
 *  - 1 UART to simulate daughterboard gyroscope 1
 *  - 1 UART to simulater daughterboard gyroscope 2
 *  - 3x2 digital INPUTS to get Hall sensors pulses
 *  - 1 digital OUTPUT to simulate power button press
 *  - 1 digital INPUT to get ERROR status
 *  
 * Project : hoverbot
 * Contact:  Rémi Pincent - remi.pincent@inria.fr
 *
 * Revision History:
 * https://github.com/OpHaCo/hoverbot.git
 * 
 * LICENSE :
 * hoverbot (c) by Rémi Pincent
 * project_name is licensed under a
 * Creative Commons Attribution-NonCommercial 3.0 Unported License.
 *
 * You should have received a copy of the license along with this
 * work.  If not, see <http://creativecommons.org/licenses/by-nc/3.0/>.
 *****************************************************************************/

/**************************************************************************
 * Include Files
 **************************************************************************/
#include "hoverboard.h"

#include <logger_config.h>
#include <IntervalTimer.h>
#include <logger.h>
#include <pid_controller.h>

/**************************************************************************
 * Manifest Constants
 **************************************************************************/

/**************************************************************************
 * Type Definitions
 **************************************************************************/

/**************************************************************************
 * Static members definitions
 **************************************************************************/
const uint8_t Hoverboard::SHORT_PRESS_DUR_MS = 100;
const uint8_t Hoverboard::GYRO_FRAME_LENGTH = 6;
const uint8_t Hoverboard::GYRO_CONTACT_CLOSED_BYTE = 85;
const uint8_t Hoverboard::GYRO_CONTACT_OPENED_BYTE = 170;
const uint16_t Hoverboard::GYRO_FRAME_START = 256;
const uint16_t Hoverboard::PID_PERIOD_MS = 200;
const uint32_t Hoverboard::HOVERBOARD_CMD_PREAMBLE = 0xABCDEF00; 
const uint8_t Hoverboard::PID_LOG_CMD_LENGTH = 24; 
const uint8_t Hoverboard::PID_LOG_CMD_ID = 1; 
const float Hoverboard::LOW_PASS_FIL_CONST = 0.2; 
const uint8_t Hoverboard::PID_INPUT_FACT = 5; 

Hoverboard* Hoverboard::_instance = NULL;

/**************************************************************************
 * Public Methods Definitions
 **************************************************************************/
Hoverboard::Hoverboard(const Hoverboard::Config& arg_config):
  _u16_powerPin(arg_config._u16_powerPin),
  _u16_powerStatPin(arg_config._u16_powerStatPin),
  _timer(),
  _e_state(OUT_OF_ENUM_STATE),
	_p_gyro1Serial(arg_config._p_gyro1Serial),
	_p_gyro2Serial (arg_config._p_gyro2Serial),
  _f_speed1(0.0),
  _f_speed2(0.0),
  _f_sensorSpeed1(0.0), 
  _f_sensorSpeed2(0.0), 
  _f_diffSpeed(0.0),
  _s16_speedRampUp(0),
  _f_commonSpeed(0.0), 
  _p_listener(NULL),
  _pid1(0.2, 0.8, 0.80, (float)(PID_PERIOD_MS)/1000.0, -1000, 1000, AUTOMATIC, DIRECT), 
  _pid2(0.2, 0.8, 0.80, (float)(PID_PERIOD_MS)/1000.0, -1000, 1000, AUTOMATIC, DIRECT), 
  _pidTimer(), 
  _u32_events(0),
  _u8_lastTickIndex(0), 
  _s32_lastTicks1(0), 
  _s32_lastTicks2(0), 
  _f_ticksFil1(0.0),
  _f_ticksFil2(0.0),
  _s32_ticks1(0),
  _s32_ticks2(0),
  _s16_gyrTarget1(0), 
  _s16_gyrTarget2(0) 
{
   
  if(arg_config._p_motor1Conf)
  {
    arg_config._p_motor1Conf->_itCbs._pfn_hall1It = Hoverboard::motor1Hall1It;
    arg_config._p_motor1Conf->_itCbs._pfn_hall2It = Hoverboard::motor1Hall2It;
    arg_config._p_motor1Conf->_itCbs._pfn_hall3It = Hoverboard::motor1Hall3It;
    arg_config._p_motor1Conf->_itCbs._pfn_timerIt = Hoverboard::motor1TimerIt;
    _hallSensor1 = BrushlessHallSensor(*arg_config._p_motor1Conf);
    _has_motor1HallSensor = true;
  }
  else
  {
    /** Do not use sensor */
    _has_motor1HallSensor = false;
  }
  
  if(arg_config._p_motor2Conf)
  {
    arg_config._p_motor2Conf->_itCbs._pfn_hall1It = Hoverboard::motor2Hall1It;
    arg_config._p_motor2Conf->_itCbs._pfn_hall2It = Hoverboard::motor2Hall2It;
    arg_config._p_motor2Conf->_itCbs._pfn_hall3It = Hoverboard::motor2Hall3It;
    arg_config._p_motor2Conf->_itCbs._pfn_timerIt = Hoverboard::motor2TimerIt;
    _hallSensor2 = BrushlessHallSensor(*arg_config._p_motor2Conf);
    _has_motor2HallSensor = true;
  }
  else
  {
    /** Do not use sensor */
    _has_motor2HallSensor = false;
  }
  _instance = this;
}
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

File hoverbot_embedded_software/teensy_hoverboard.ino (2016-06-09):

static int16_t currPos = 0;

#define LOG_SERIAL                        Serial
#define DAUGHTER_BOARD_SERIAL             Serial2
#define DAUGHTER_BOARD_SERIAL_SIM_L       Serial1
#define DAUGHTER_BOARD_SERIAL_SIM_R       Serial3

void setup() {
   LOG_SERIAL.begin(115200);
   
   DAUGHTER_BOARD_SERIAL.begin (26300, SERIAL_9N1);        // 9 bits mode
   DAUGHTER_BOARD_SERIAL_SIM_L.begin (26300, SERIAL_9N1);  // 9 bits mode
   DAUGHTER_BOARD_SERIAL_SIM_R.begin (26300, SERIAL_9N1);  // 9 bits mode
   
   LOG_SERIAL.println("start");
}

void loop() {
  //echoGoForward(0);
  daughterEcho();
  //printCurrentPos();
}

/** 
 *  echo value read from a single daughterboard to 
 *  motherboard left and right UART
 */
void daughterEcho(void)
{
  if (DAUGHTER_BOARD_SERIAL.available())
  {
    uint16_t data = DAUGHTER_BOARD_SERIAL.read();
    DAUGHTER_BOARD_SERIAL_SIM_R.write9bit(data);
    DAUGHTER_BOARD_SERIAL_SIM_L.write9bit(data);
  }
}

/** 
 *  Read current position from a single daughterboard
 */
void printCurrentPos(void)
{
    if (DAUGHTER_BOARD_SERIAL.available()) {
      int16_t readPos = 0;

      /** begin of frame */
      if(DAUGHTER_BOARD_SERIAL.read() == 256)
      { 
        /** get angle LSB (8 bits) */
        while (!DAUGHTER_BOARD_SERIAL.available()){};
        /** ninth bits not used */
        readPos |= DAUGHTER_BOARD_SERIAL.read() & 0xFF;

        /** get angle MSB (8 bits) */
        while (!DAUGHTER_BOARD_SERIAL.available()){};
        /** ninth bits not used */
        readPos |= (DAUGHTER_BOARD_SERIAL.read() & 0xFF) << 8;
        
        if(readPos != currPos)
        {
          currPos = readPos;
          LOG_SERIAL.println(readPos);
        }
      }
      else
      {
      }
  }
  else
  {
    //LOG_SERIAL.println("nothing to read");
  }
}

/** 
 *  Read current position from a single daughterboard and 
 *  control both uard to go forward
 */
void echoGoForward(uint16_t speed)
{
    if (DAUGHTER_BOARD_SERIAL.available()) {
      int16_t readPos = 0;

      /** begin of frame */
      if(DAUGHTER_BOARD_SERIAL.read() == 256)
      { 
        /** get angle LSB (8 bits) */
        while (!DAUGHTER_BOARD_SERIAL.available()){};
        /** ninth bits not used */
        readPos |= DAUGHTER_BOARD_SERIAL.read() & 0xFF;

        /** get angle MSB (8 bits) */
        while (!DAUGHTER_BOARD_SERIAL.available()){};
        /** ninth bits not used */
        readPos |= (DAUGHTER_BOARD_SERIAL.read() & 0xFF) << 8;

        /** echo current frame on both uart with forward direction */
        uint16_t lFrame[6] = {256, readPos & 0xff, readPos >> 8 & 0xff, readPos & 0xff, readPos >> 8 & 0xff, 85};
        uint16_t rFrame[6] = {256, (-readPos) & 0xff, (-readPos) >> 8 & 0xff, (-readPos) & 0xff, (-readPos) >> 8 & 0xff, 85};

        for(uint8_t index = 0; index < 6; index++)
        {
          DAUGHTER_BOARD_SERIAL_SIM_R.write9bit(rFrame[index]);
          DAUGHTER_BOARD_SERIAL_SIM_L.write9bit(lFrame[index]); 
        }
        
        if(readPos != currPos)
        {
          currPos = readPos;
          LOG_SERIAL.println(readPos);
        }
      }
      else
      {
      }
  }
  else
  {
    //LOG_SERIAL.println("nothing to read");
  }  
}

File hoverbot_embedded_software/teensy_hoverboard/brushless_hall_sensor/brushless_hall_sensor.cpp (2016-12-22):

/******************************************************************************
 * @file    brushless_hall_sensor.cpp
 * @author  Rémi Pincent - INRIA
 * @date    24/11/2016
 *
 * @brief Get sensor speed in deg/s from some hall sensors
 *
 * Project : hoverbot
 * Contact:  Rémi Pincent - remi.pincent@inria.fr
 *
 * Revision History:
 * https://github.com/OpHaCo/hoverbot.git 
 * 
 * LICENSE :
 * hoverbot (c) by Rémi Pincent
 * hoverbot is licensed under a
 * Creative Commons Attribution-NonCommercial 3.0 Unported License.
 *
 * You should have received a copy of the license along with this
 * work.  If not, see <http://creativecommons.org/licenses/by-nc/3.0/>.
 *****************************************************************************/

/**************************************************************************
 * Include Files
 **************************************************************************/
#include "brushless_hall_sensor.h"

#include <Arduino.h>

/**************************************************************************
 * Manifest Constants
 **************************************************************************/
/**************************************************************************
 * Type Definitions
 **************************************************************************/

/**************************************************************************
 * Global Variables
 **************************************************************************/

/**************************************************************************
 * Static Variables
 **************************************************************************/
/** To customize depending on your hall sensors */
const float BrushlessHallSensor::NB_TICKS_ROTA = 44.7;
const uint16_t BrushlessHallSensor::TIMER_PERIOD_MS = 2500;
/**************************************************************************
 * Macros
 **************************************************************************/

/**************************************************************************
 * Local Functions Declarations
 **************************************************************************/
/**************************************************************************
 * Public Functions Defintions
 **************************************************************************/

BrushlessHallSensor::BrushlessHallSensor(void) :
  _config(),
  _s32_hallTicks(0),
  _s32_periodHallTicks(0),
  _s32_lastPeriodHallTicks(0),
  _e_lastHallSensed(BrushlessHallSensor::OUT_OF_ENUM_SENSOR),
  _captureTimer()
{
}

BrushlessHallSensor::BrushlessHallSensor(const Config& arg_config):BrushlessHallSensor()
{
  _config = arg_config;
}

void BrushlessHallSensor::startSensing(void)
{
  BrushlessHallSensor::_s32_hallTicks = 0;
  BrushlessHallSensor::_e_lastHallSensed = BrushlessHallSensor::OUT_OF_ENUM_SENSOR;

  pinMode(_config._u8_hall1Pin, INPUT_PULLUP);
  pinMode(_config._u8_hall2Pin, INPUT_PULLUP);
  pinMode(_config._u8_hall3Pin, INPUT_PULLUP);
  
  
  attachInterrupt(_config._u8_hall1Pin, _config._itCbs._pfn_hall1It, RISING); 
  attachInterrupt(_config._u8_hall2Pin, _config._itCbs._pfn_hall2It, RISING); 
  attachInterrupt(_config._u8_hall3Pin, _config._itCbs._pfn_hall3It, RISING); 
  
  _captureTimer.begin(_config._itCbs._pfn_timerIt, BrushlessHallSensor::TIMER_PERIOD_MS*1000);
  _s32_periodHallTicks = 0;
  _s32_lastPeriodHallTicks = 0;
}

void BrushlessHallSensor::stopSensing(void)
{
  _captureTimer.end();
  detachInterrupt(_config._u8_hall1Pin);
  detachInterrupt(_config._u8_hall2Pin);
  detachInterrupt(_config._u8_hall3Pin);
}

float BrushlessHallSensor::getSpeed(void)
{
  /** No need to do a copy to avoid a concurrent write, _s32_lastPeriodHallTicks is a world */
  return PI*(((float)_s32_lastPeriodHallTicks*1000)/(float)TIMER_PERIOD_MS)/NB_TICKS_ROTA;
}
/**************************************************************************
 * Private Functions Definitions
 **************************************************************************/
void BrushlessHallSensor::hall1It(void)
{
  detachInterrupt(_config._u8_hall1Pin); 
  /** reject spikes */
  if(digitalRead(_config._u8_hall1Pin) &&
      ((digitalRead(_config._u8_hall2Pin) && !digitalRead(_config._u8_hall3Pin))
       || (!digitalRead(_config._u8_hall2Pin) && digitalRead(_config._u8_hall3Pin))))
  {

    if(_e_lastHallSensed == BrushlessHallSensor::SENSOR_3)
    {
      _s32_hallTicks++;
    }
    else if(_e_lastHallSensed == BrushlessHallSensor::SENSOR_2)
    {
      _s32_hallTicks--;
    }
    _e_lastHallSensed = BrushlessHallSensor::SENSOR_1;
  }
  attachInterrupt(_config._u8_hall1Pin, _config._itCbs._pfn_hall1It, RISING); 
}

void BrushlessHallSensor::hall2It(void)
{
  detachInterrupt(_config._u8_hall2Pin); 
  /** reject spikes */
  if(digitalRead(_config._u8_hall2Pin) &&
      ((digitalRead(_config._u8_hall1Pin) && !digitalRead(_config._u8_hall3Pin))
       || (!digitalRead(_config._u8_hall1Pin) && digitalRead(_config._u8_hall3Pin))))
  {
    if(_e_lastHallSensed == BrushlessHallSensor::SENSOR_1)
    {
      _s32_hallTicks++;
    }
    else if(_e_lastHallSensed == BrushlessHallSensor::SENSOR_3)
    {
      _s32_hallTicks--;
    }
    _e_lastHallSensed = BrushlessHallSensor::SENSOR_2;
  }
  attachInterrupt(_config._u8_hall2Pin, _config._itCbs._pfn_hall2It, RISING); 
}

void BrushlessHallSensor::hall3It(void)
{
  detachInterrupt(_config._u8_hall3Pin); 
  /** reject spikes */
  if(digitalRead(_config._u8_hall3Pin) &&
      ((digitalRead(_config._u8_hall1Pin) && !digitalRead(_config._u8_hall2Pin))
       || (!digitalRead(_config._u8_hall1Pin) && digitalRead(_config._u8_hall2Pin))))
  {
    if(_e_lastHallSensed == BrushlessHallSensor::SENSOR_2)
    {
      _s32_hallTicks++;
    }
    else if(_e_lastHallSensed == BrushlessHallSensor::SENSOR_1)
    {
      _s32_hallTicks--;
    }
    _e_lastHallSensed = BrushlessHallSensor::SENSOR_3;
  }
  attachInterrupt(_config._u8_hall3Pin, _config._itCbs._pfn_hall3It, RISING); 
}


void BrushlessHallSensor::timerIt(void){
  _s32_lastPeriodHallTicks = _s32_hallTicks - _s32_periodHallTicks;
  _s32_periodHallTicks = _s32_hallTicks;
}

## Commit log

2016-06-09 First tests with teensy3.1
2016-11-25 Add hall decoder
2016-12-07 Workaround to handle sensor IT in objects
2016-12-16 UART speed change
2016-12-16 Squashed 'hoverbot_embedded_software/teensy_hoverboard/logger/' content from commit c66ec33
    git-subtree-dir: hoverbot_embedded_software/teensy_hoverboard/logger
    git-subtree-split: c66ec33e79c361d81ed4afd4e6b1320883942a62
2016-12-19 Add rampUp duration argument to setSpeed. Add timestamp in UART console
2016-12-22 Add hall detection imgs
2016-12-22 debug hall sensor => add schmitt trigger
2016-12-23 Add timestamp in uart terminal
2016-12-23 Check power status, add motor1 hall sensors
2017-03-22 Squashed 'hoverbot_embedded_software/teensy_hoverboard/pid_controller/' content from commit d9643c1
    git-subtree-dir: hoverbot_embedded_software/teensy_hoverboard/pid_controller
    git-subtree-split: d9643c185318c6f10d6917bc4cfb9b32fbda8fb0
2017-03-24 Scrolling bug. Split ontent of text widgets into multiple widgets
    [commander.py, hoverboard_uart_control.py]
2017-03-31 Add motor monitor
2017-04-05 Add filtered_input
2017-04-05 Add PID, PID debug for both wheels
2017-04-05 log gyro status
2017-04-26 Add command to get current ticks
2018-05-23 Refer to actively developed repository
    I hope this is okay to you, because your repository is currently the most popular, but contains only information and proof-of-concept, while the one I linked will give you a complete and working hove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
